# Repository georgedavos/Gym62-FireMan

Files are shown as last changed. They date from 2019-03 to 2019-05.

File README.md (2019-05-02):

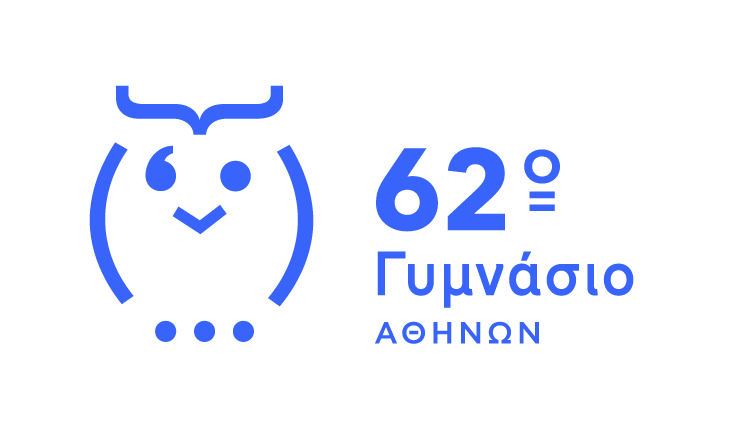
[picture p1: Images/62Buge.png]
62 Γυμνάσιο Αθηνών


# Gym62-FireMan
## Αυτόνομο Όχημα Ανίχνευσης Θέσης Πυρκαϊάς

Η ομάδα ρομποτικής του 62ου Γυμνασίου Αθηνών, μελετά και κατασκευάζει ένα  αυτοκινούμενο όχημα, το οποίο έχει ως σκοπό να επιτηρεί και να προστατεύει ένα δάσος από πυρκαϊά, και παράλληλα να μεταδίδει τα δεδομένα διαμέσου WiFi σημείου πρόσβασης που διαθέτει ενσωματωμένο.

Το Gym62-FireMan βασίστηκε σε ένα ερπυστριοφόρο σκάφος εκσκαφέα, το οποίο τροποποιήθηκε κατάλληλα για τις ανάγκες του έργου, ελάχιστης αξίας, και σε έναν ειδικό αισθητήρα παράταξης υπερύθρων ακτίνων. 

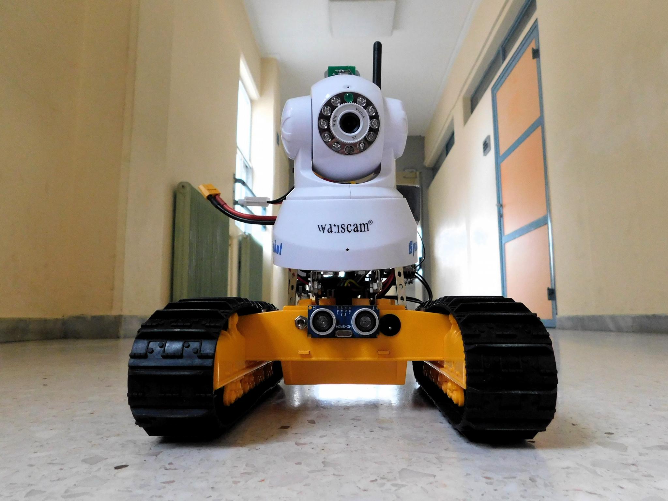
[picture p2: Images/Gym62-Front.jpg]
Gym62 Front


Gym62 Animated

## Περιγραφή πλοήγησης

 Το σύστημα βασίζεται σε ένα αισθητήρα παράταξης υπέρυθρων ακτίνων.
 
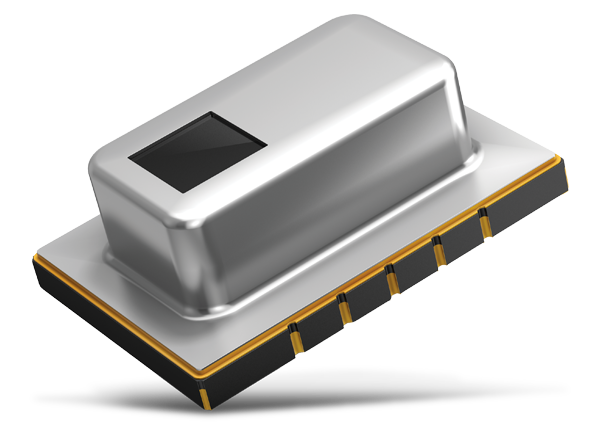
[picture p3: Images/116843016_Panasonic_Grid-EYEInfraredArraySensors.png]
Grid Eye
 
 
Ο αισθητήρας παράταξης είναι δομημένος σε ένα πίνακα 8*8 στοιχείων, δίνοντας 64 ανεξάρτητα σημεία μέτρησης της θερμότητας.
 Χωρίζοντας τον αισθητήρα σε 8 ζώνες ορίζοντα, ανιχνεύεται ο ορίζοντας στον οποίο εμφανίζεται η μέγιστη θερμότητα. Με βάση τον επιλεγμένο ορίζοντα, το όχημα μεταβάλει την ταχύτητα των ερπυστριών συνεχώς, αναλογικά σε σχέση πάντα με την θέση της μέγιστης θερμότητας στον επιλεγμένο ορίζοντα.
 Αυτή ή συνεχώς μεταβαλλόμενη ταχύτητα των ερπυστριών οδηγεί με μεγάλη ακρίβεια το όχημα στην θέση της πυρκαϊάς.   
 Πιο συγκεκριμένα το όχημα περιστρέφεται συνεχώς γύρω από τον εαυτό του μετρώντας τα θερμικά φορτία του πεδίου ορατότητας. Εάν κατά την περιστροφή, μετρηθεί θερμικό φορτίο μεγαλύτερο από το προκαθορισμένο ( Triger ), τότε σταματάει και κινείται προς αυτό, διορθώνοντάς συνεχώς την πορεία του φροντίζοντας να την διατηρεί σταθερή και ευθεία μπροστά με κέντρο πάντα το μέγιστο θερμικό φορτίο, επικοινωνώντας ταυτόχρονα με το κέντρο ελέγχου μεταδίδοντας σήματα σχετικά με τις λειτουργίες του και αποδέχεται ρυθμίσεις πλοήγησης.

## Λογισμικό Κέντρου Ελέγχου.
Το Gym62RCNT είναι μια εφαρμογή τηλεμετρίας για τον έλεγχο και της ρυθμίσεις του οχήματος.
Αναπτύσσεται σε περιβάλλον NetBeans 8.6 Java JDK 1.8.
Για να τρέξετε την εφαρμογή χωρίς την χρήση Του  NetBeans. Εγκαταστήστε το  java run time environment στο συστημά σας και τρέξτε το αρχείο  Gym62RCNT.jar

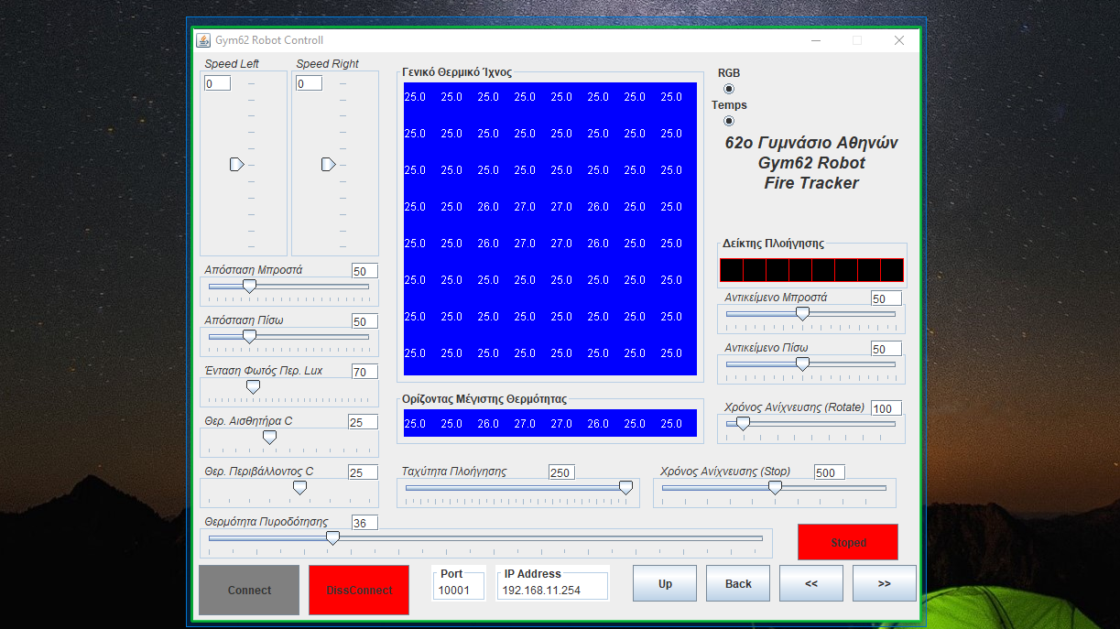
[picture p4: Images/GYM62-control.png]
Gym62 Control


## Κύκλωμα Gym62-MM3
Πρόκειται για ένα ηλεκτρονικό κύκλωμα επέκτασης οποιασδήποτε συμβατού Arduino πού λειτουργεί ως βάση σύνδεσης όλων των περιφερειακών συστημάτων τηλεμετρίας και τηλεκήνησης.
Για την ανάπτυξη του χρησιμοποιήθηκε το Ανοιχτό λογισμικό  KiCad IDE.

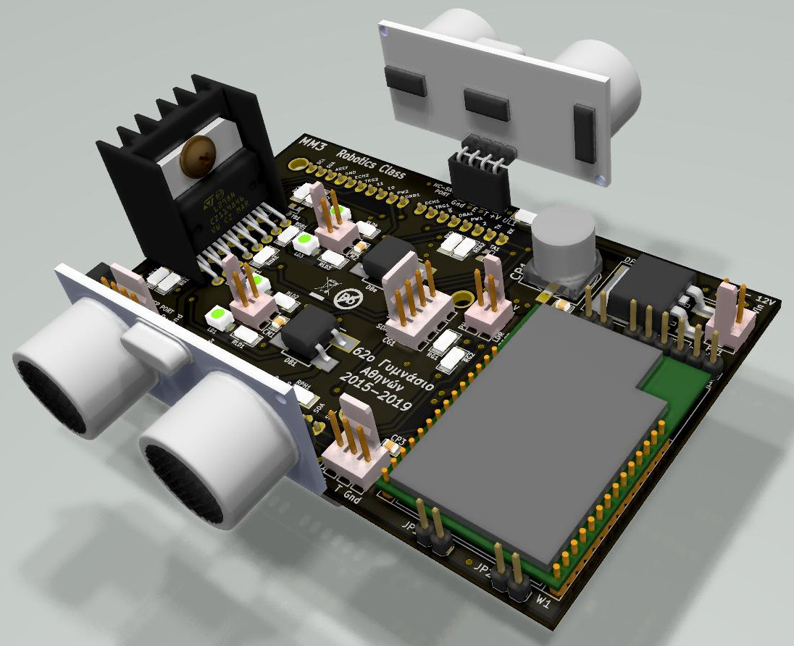
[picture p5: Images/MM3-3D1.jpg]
MM3-1


## Λεπτομέρεις Περιγραφές.
Περιγραφή περιεχομένων των αρχείων και των φακέλων που έχουν ενσωματωθεί στο github βρίσκεται σε αρχείο με όνομα "GYM62-FIREMAN-TreeOfFiles-Description" στον ίδιο κατάλογο με το παρόν ( https://github.com/georgedavos/Gym62-FireMan/blob/master/GYM62-FIREMAN-TreeOfFiles-Description.odt ).

Δείτε το βίντεο του έργου στο κανάλι youtube του σχολείου μας (62ο Γυμνάσιο Αθήνας)

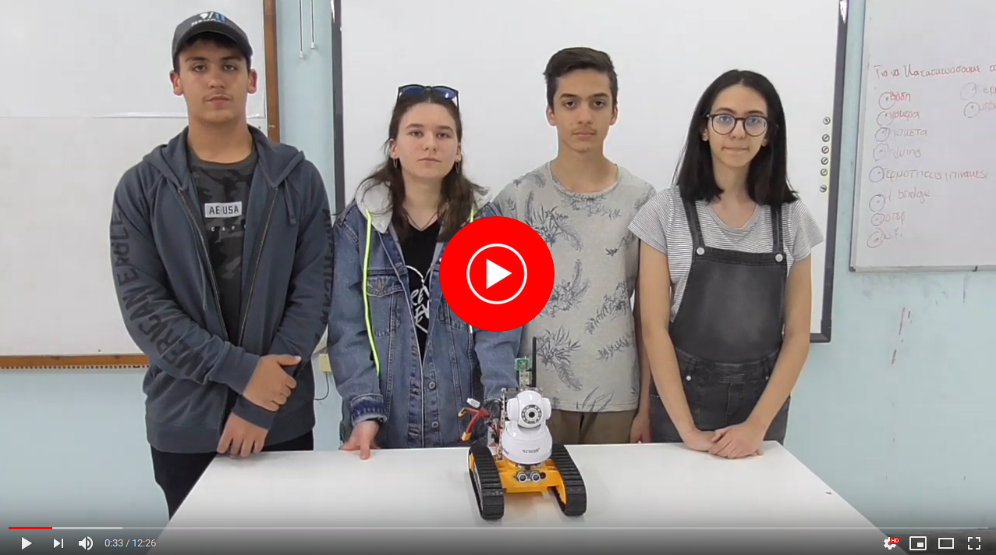
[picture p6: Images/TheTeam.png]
The Team (https://www.youtube.com/watch?v=zAY0CPyWmjs)


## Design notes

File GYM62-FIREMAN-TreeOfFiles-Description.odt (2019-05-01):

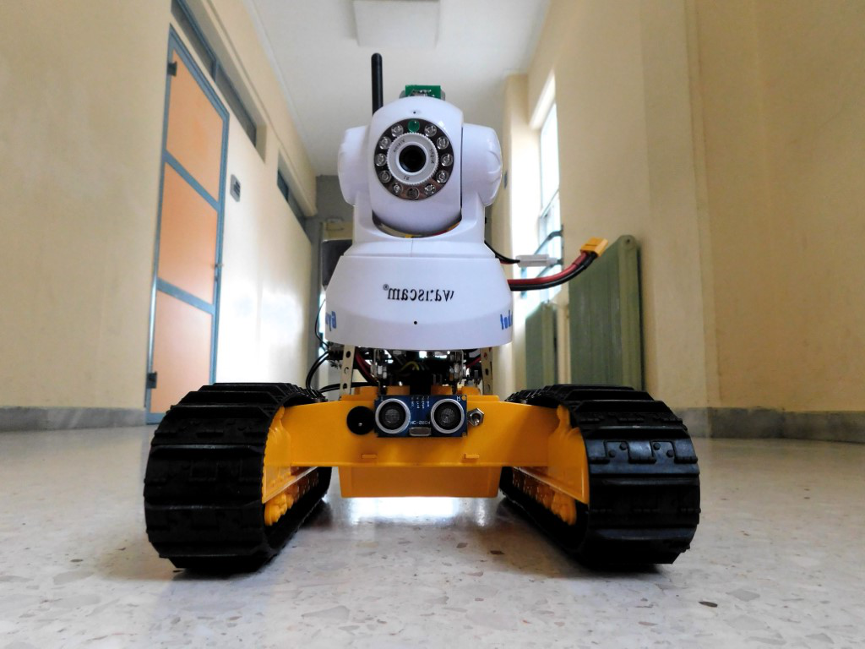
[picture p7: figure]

Περιγραφή δένδρου και σημαντικών αρχείων στο github του 62GYM-FIREMAN

Στο github του έργου (https://github.com/georgedavos/Gym62-FireMan)

Στον βασικό κατάλογο εμφανίζονται τα παρακάτω:

Αρχείο README.md είναι μια σύντομη περιγραφή του έργου που παρουσιάζεται.

Επίσης οι φάκελλοι:

- Arduino-Code/Gim62_MM3FireMan_A4 (https://github.com/georgedavos/Gym62-FireMan/tree/master/Arduino-Code/Gim62_MM3FireMan_A4) φάκελλος που περιέχει
- Το αρχείο Gim62_MM3FireMan_A4.ino (https://github.com/georgedavos/Gym62-FireMan/blob/master/Arduino-Code/Gim62_MM3FireMan_A4/Gim62_MM3FireMan_A4.ino) με τον πηγαίο κώδικα που έχει φορτωθεί στο Arduino με πλήρη σχόλια για κάθε λειτουργία που έχει ενσωματωθεί.
- Documents (https://github.com/georgedavos/Gym62-FireMan/tree/master/Documents) φάκελλος που περιέχει τις παρουσιάσεις και τις περιγραφές του έργου.
- Το αρχείο Περιγραφή Εργου Gym62-FireMan.odt (https://github.com/georgedavos/Gym62-FireMan/blob/master/Documents/Περιγραφή%20Εργου%20Gym62-FireMan.odt) έγγραφο με την γενική πιο λεπτομερή περιγραφή του έργου.
- Το αρχείο 62GYM-FIREMAN Κόστος Υλικών.odt (https://github.com/georgedavos/Gym62-FireMan/blob/master/Documents/62GYM-FIREMAN%20Κόστος%20Υλικών.odt) έγγραφο με το κόστος και την λεπτομερή λίστα των υλικών τόσο της πλακέτας GYM62-MM3 όσο και του συνολικού έργου.
- Το αρχείο Gym62-CameraDescription.odp (https://github.com/georgedavos/Gym62-FireMan/blob/master/Documents/Gym62-CameraDescription.odp) με την παρουσίαση των λειτουργιών και των τεχνικών χαρακτηριστικών της ενσωματωμένης κάμερας PLT-VGA
- To αρχείο Gym62-MM3_Description-final.odp (https://github.com/georgedavos/Gym62-FireMan/blob/master/Documents/Gym62-MM3_Description-final.odp) με την παρουσίαση των λειτουργιών και συνδέσεων της πλακέτας επέκτασης για ARDUINO GYM62-MM3 που έχει υλοποιηθεί στο σχολείο μας.
- Το αρχείο Gym62-WIFI&Αισθητήρας θερμότητας.odp (https://github.com/georgedavos/Gym62-FireMan/blob/master/Documents/Gym62-WIFI%26Αισθητήρας%20θερμότητας.odp) με την παρουσίαση των λειτουργιών της μονάδας WIFI και του αισθητήρα ανίχνευσης θερμικού φορτίου GRID EYE.
- Το αρχείο Gym62-Τηλεμετρία-Τηλεχειρισμός.odp (https://github.com/georgedavos/Gym62-FireMan/blob/master/Documents/Gym62-Τηλεμετρία-Τηλεχειρισμός.odp) με την παρουσίαση του κέντρου ελέγχου του ρομπότ της διαδικασίας της τηλεμετρίας και του τηλεχειρισμού του, όπως επίσης τα πρωτόκολλα που έχουν υλοποιηθεί για την μετάδοση δεδομένων από και προς το ρομπότ.
- Το αρχείο GYM62-FIREMAN-OER-ver2.pdf (https://github.com/georgedavos/Gym62-FireMan/blob/master/Documents/GYM62-FIREMAN-OER-ver2.pdf) που περιέχει τα στοιχεία του έργου με βάση το πρότυπο OER
- Gym62-MM3-Circuit (https://github.com/georgedavos/Gym62-FireMan/tree/master/Gym62-MM3-Circuit) φάκελλος που περιέχει:
    - MM3-Production (https://github.com/georgedavos/Gym62-FireMan/tree/master/Gym62-MM3-Circuit/MM3-Production) φάκελλος που περιέχει τα αρχεία σχεδιασμού της πλακέτας ως Project του KICAD ( EDA ) ( MM3.pro (https://github.com/georgedavos/Gym62-FireMan/blob/master/Gym62-MM3-Circuit/MM3.pro) ) ( MM3.sch (https://github.com/georgedavos/Gym62-FireMan/blob/master/Gym62-MM3-Circuit/MM3.sch) ) (MM3.kicad_pcb (https://github.com/georgedavos/Gym62-FireMan/blob/master/Gym62-MM3-Circuit/MM3.kicad_pcb)) και τα αρχεία GERBER για την παραγωγή της.
    - datasheets (https://github.com/georgedavos/Gym62-FireMan/tree/master/Gym62-MM3-Circuit/datasheets) : φάκελλος που περιέχει τα datasheets των βασικών εξαρτημάτων που χρησιμοποιήθηκαν – Είναι για τον μελλοντικό προγραμματιστή που θα βελτιώσει και θα αναπτύξει περαιτέρω το έργο
    - rescue-backup (https://github.com/georgedavos/Gym62-FireMan/tree/master/Gym62-MM3-Circuit/rescue-backup) : φάκελλος που το λέει και το όνομά του !!!!!
- Gym62RCNT (https://github.com/georgedavos/Gym62-FireMan/tree/master/Gym62RCNT) φάκελλος που περιέχει όλα τα αρχεία ανάπτυξης του κέντρου ελέγχου του ρομπότ ως Project σε ολοκληρωμένο περιβάλλον ανάπτυξης NetBeans IDE
- src (https://github.com/georgedavos/Gym62-FireMan/tree/master/Gym62RCNT/src) : φάκελλος που περιέχει τον source code σε Java της εφαρμογής του κέντρου ελέγχου
- Το αρχείο Gym62RCNT.jar (https://github.com/georgedavos/Gym62-FireMan/blob/master/Gym62RCNT/Gym62RCNT.jar) με την εφαρμογή του κέντρου ελέγχου υλοποιημένη σε JAVA
- Το αρχείο Gym62-Screen-Shot.jpg (https://github.com/georgedavos/Gym62-FireMan/blob/master/Gym62RCNT/Gym62-Screen-Shot.jpg) είναι μια φωτογραφία screenshot της εφαρμογής προς ενημέρωση
- Τα υπόλοιπα αρχεία και φάκελλοι είναι για τον προγραμματιστή της JAVA που θα βελτιώσει και θα αναπτύξει περαιτέρω το έργο (build (https://github.com/georgedavos/Gym62-FireMan/tree/master/Gym62RCNT/build), dist (https://github.com/georgedavos/Gym62-FireMan/tree/master/Gym62RCNT/dist), nbproject (https://github.com/georgedavos/Gym62-FireMan/tree/master/Gym62RCNT/nbproject) )
- Images (https://github.com/georgedavos/Gym62-FireMan/tree/master/Images) που περιέχει όλες τις φωτογραφίες που έχουν χρησιμοποιηθεί στα documents του έργου

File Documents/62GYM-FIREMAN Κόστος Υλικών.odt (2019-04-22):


Κόστος υλικών GYM62-FIREMAN

α/α | Περιγραφή Υλικού | Ενδεικτική τιμή λιανικής ( € )
1 | Όχημα ερπυστριοφόρο – μόνο το σκάφος από τροποποιημένο εκσκαφέα με λειτουργία των ερπυστριών και των μοτέρ τους, μικρής αξίας. | 15,00 €
2 | Arduino Uno ver3 | 7,00 €
3 | GYM62-MM3 Shield για το Arduino για εκπαιδευτικούς σκοπούς με την γέφυρα “Η” για τον έλεγχο των μοτέρ L298 DUAL FULL-BRIDGE DRIVER και λοιπά εξαρτήματα όπως περιγράφεται παρακάτω ** με υποδοχές για αισθητήρες για αποφυγή του πλήθους των καλωδιώσεων, σχεδιασμένο σε Kicad με πολύ χαμηλό κόστος παραγωγής. | 7,00 €
4 | Αναλογικός Αισθητήρας θερμοκρασίας περιβάλλοντος LM-35. | 0,40 €
5 | Αισθητήρας φωτός (φωτοαντίσταση LDR) | 0,50 €
6 | Αισθητήρας παράταξης υπερύθρων ακτίνων για την μέτρηση θερμότητας Grid Eye Panasonic. | 15,00 €
7 | Αισθητήρας Υπερήχων HC-SR 04 (2 τεμάχια) | 4,00 €
8 | Διεπαφή επικοινωνίας WIFI – Access Point HLK-RM 04 με την αντίστοιχη κεραία | 15,00 €
9 | Διεπαφή επικοινωνίας Bluetooth HC-06 (προαιρετική) | 2,50 €
10 | Web - Κάμερα μετάδοσης εικόνας Pan-Tilt-Zoom (κινούμενης κεφαλής) σε ανάλυση απλής VGA μικρής αξίας. | 25,00 €
11 | Μπαταρία Lipo 11,1V χαμηλού ρεύματος εκκίνησης | 28,00 €
12 | Στοιχεία μεταλλικών κατασκευών από παιχνίδια για τις στηρίξεις των υλικών | 3,00 €
13 | Καλώδια, ακροφύσια | 2,00 €
13 | Διακόπτες ηλεκτρικών και ηλεκτρονικών συνδέσεων. | 1,00 €
| ΣΥΝΟΛΟ | 106,4 €

Όλα τα υλικά αναφέρονται με λεπτομέρεια τόσο παρακάτω όσο και στα σχέδια της πλακέτας ΜΜ3 που έχουν μπεί στο github (https://github.com/georgedavos/Gym62-FireMan/tree/master/Gym62-MM3-Circuit/MM3-Production)του έργου (https://github.com/georgedavos/Gym62-FireMan/tree/master/Gym62-MM3-Circuit/MM3-Production) (https://github.com/georgedavos/Gym62-FireMan/tree/master/Gym62-MM3-Circuit/MM3-Production)

** Λίστα υλικών επί της πλακέτας επέκτασης στην επόμενη σελίδα μαζί με τους κατασκευαστές κάθε είδους

** Υλικά πλακέτας 62GYM-MM3 Shield

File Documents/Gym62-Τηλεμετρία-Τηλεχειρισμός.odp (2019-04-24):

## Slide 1

η ομαδα ρομποτικησ στο


παρουσιαζει

Gym62_FireMan

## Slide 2

Gym62_Robot

Gym62_FireMan

Gym62_FireMan

ΠΕΡΙΓΡΑΦΗ κεντρου ελεγχου και πρωτοκολλου επικοινωνιασ

Μαθητές:

Βενέτης Αναστάσης

Μαλανκά Αλεξάνδρα

Παναγιωτάκης Βαγγέλης

Σπυροπούλου Ζωή

Καθηγητές-Μέντορες:

Δάβος Γεώργιος

Βλαστός Αθανάσιος

Μπερερής Σπύρος

## Λειτουργία και πρωτόκολλο επικοινωνίας

Gym62_Robot

- Το ρομπότ μας επικοινωνεί με κέντρο ελέγχου τηλεμετρίας και τηλεχειρισμού, που εκτελείται σε ένα laptop ή σε desktop με ασύρματη κάρτα δικτύου.
- Ο κάθε χείριστης του ρομπότ μπορεί να λαμβάνει δεδομένα από το ρομπότ αλλά και να ρυθμίζει τις λειτουργίες του μέσα από ένα πρόγραμμα σε Java που έχουμε δημιουργήσει με την βοήθεια του μέντορά μας Βλαστού Αθανάσιου.
- Η μετάδοση των δεδομένων από και προς το κέντρο ελέγχου γίνεται μέσω πρωτοκόλλου μετάδοσης data που σχεδιάστηκε ειδικά για το Gym62-Fireman

Gym62_FireMan

## Τηλεμετρία

Gym62_Robot

  Το ρομπότ επικοινωνεί με τον πίνακα ελέγχου και στέλνει πληροφορίες η οποίες αφορούν την λειτουργία του :
- Ταχύτητα και κατεύθυνση (δεξιάς και αριστερής ερπύστριας)
- Θερμοκρασία περιβάλλοντος του ρομπότ
- Απόσταση από εμπόδια (αισθητήρας υπερήχων μπροστά και πίσω)
- Φωτεινότητα περιβάλλοντος
- Θερμοκρασίες που ανιχνεύει ο θερμικός ανιχνευτής GridEye
- Δείκτης αυτόματης πλοήγησης – κατεύθυνσης κίνησης

Gym62_FireMan

## Τηλεχειρισμός

Gym62_Robot

  Μέσω του πίνακα ελέγχου μπορεί κανείς να ελέγξει κάποιες λειτουργίες του ρομπότ χωρίς αλλαγή στον κώδικα :
- Ταχύτητα και κατεύθυνση ερπυστριών σε ποσοστό – σημειώνεται ότι αρνητικές τιμές σημαίνει κίνηση προς τα πίσω και θετικές κίνηση εμπρός.
- Ρύθμιση χρόνου ταχύτητας περιστροφής στην φάση ανίχνευσης
- Κατώφλι Θερμοκρασίας ανίχνευσης

Gym62_FireMan

## Τηλεκίνηση

Gym62_Robot

  Το ρομπότ σταματάει να ακολουθεί το πρόγραμμα και μπορεί να ελεγχθεί η κατεύθυνση του από τον πινάκα ελέγχου . Οι κινήσεις που μπορεί να εκτελέσει ρυθμίζοντας το είδος της κίνησης και την ταχύτητα κίνησης των ερπυστριών είναι οι εξής
- Μπροστά (θετικές τιμές)
- Πίσω (αρνητικές τιμές)
- Γύρω από τον άξονα του, δεξιά (αντίστροφη κίνηση ερπυστριών)
- Γύρω από τον άξονα του, αριστερά (αντίστροφη κίνηση ερπυστριών)

Gym62_FireMan

## Πρωτόκολλο επικοινωνίας Τηλεμετρίας

Gym62_Robot

  Η μετάδοση των δεδομένων από το ρομπότ προς το κέντρο ελέγχου ασύρματα γίνεται, όπως φαίνεται και στον ενσωματωμένο σχολιασμό του κώδικα, με τη χρήση strings μέσω πακέτων μετάδοσης του προτύπου UART του TCP/IP. Aνάλογα με το είδος των δεδομένων ξεκινούν με:
1. !tmp- : Θερμοκρασία
2. !lgt- : Φωτεινότητα
3. !spr- & !spl- :Ταχύτητα δεξιάς & αριστερής ερπύστριας σε ποσοστό επί της ισχύος του μοτέρ
4. !dtf- & !dtb- : Αποστάσεις μπροστά & πίσω αισθητήρα υπερήχων σε cm
5. !htt- : Θερμοκρασία του περιβάλλοντος του Ρομπότ
  και ακολουθούν μετά από αυτά οι αντίστοιχες τιμές πχ ‘!tmp-22’

Gym62_FireMan

## Πρωτόκολλο επικοινωνίας Τηλεχειρισμού

Gym62_Robot

Gym62_FireMan

  Η μετάδοση των δεδομένων από το κέντρο ελέγχου προς το ρομπότ ασύρματα γίνεται όπως φαίνεται και στον ενσωματωμένο σχολιασμό του κώδικα με τη χρήση strings μέσω πακέτων μετάδοσης του προτύπου UART του TCP/IP. Aνάλογα με το είδος των δεδομένων ξεκινούν με:
- !spd- :Ταχύτητα Ρομπότ σε ποσοστό της ισχύος του μοτέρ (50%)
- !tme- : Χρονόμετρο σε sec
- !trg- : Κατώφλι Θερμοκρασίας ανίχνευσης θερμικού στόχου σε oC
  και ακολουθούν μετά από αυτά οι αντίστοιχες τιμές πχ ‘!spd-50’

## Πίνακας ελέγχου (Τηλεμετρία)

Gym62_Robot

Gym62_FireMan

1.Θερμοκρασία περιβάλλοντος

2.Φωτεινότητα περιβάλλοντος

3.Ταχύτητα και φορά δεξιάς & αριστερής ερπύστριας (+ ή -% )

4.Αποστάσεις μπροστά & πίσω αισθητήρα

5.Θερμοκρασία περιβάλλοντος (του Ρομπότ)

3

4

2

5

1

## Πίνακας ελέγχου (Τηλεδιαχείριση)

Gym62_Robot

Gym62_FireMan

1.Ταχύτητα κίνησης Ρομπότ (0-255)

2.Χρόνος ρύθμισης ταχύτητας περιστροφής στη φάση Ανίχνευσης

3.Κατώφλι Θερμοκρασίας που θα ανιχνεύει το ρομπότ

4. Κουμπί εκκίνησης και στάσης του ρομπότ με αλλαγή χρώματος και λεζάντας σε λειτουργία

5. Εισαγωγή διεύθυνσης IP του ρομπότ και πόρτας μετάδοσης δεδομένων

6. Κουμπιά σύνδεσης και αποσύνδεσης με το ρομπότ με αλλαγή χρώματος και λεζάντας

1

2

3

4

5

6

## Πίνακας ελέγχου (Τηλεχειρισμός κίνησης)

Gym62_Robot

Gym62_FireMan

Όταν το ρομπότ δεν είναι σε φάση ανίχνευσης (stopped mode) τότε μπορούμε να διαχειριστούμε την κίνησή του

1.φάση stpped mode – δεν ανιχνεύει φωτιά

2.Κουμπιά χειρισμού της κίνησης με τη σειρά μπρός (up), πίσω back), αριστερά (<<) και δεξιά (>>)

1

2

## Πίνακας ελέγχου (Grid Eye)

Gym62_Robot

Gym62_FireMan

1.Τιμές θερμικού ανιχνευτή (Grid Eye) και γραμμή μέγιστων θερμοκρασιών (Ορίζοντας Μέγιστης Θερμότητας)

2.Δείκτης πλοήγησης – κατεύθυνσης κίνησης (auto navigation feedback)

1

2

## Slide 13

Gym62_Robot

Gym62_FireMan

ΕΥΧΑΡΙΣΤΟΥΜΕ

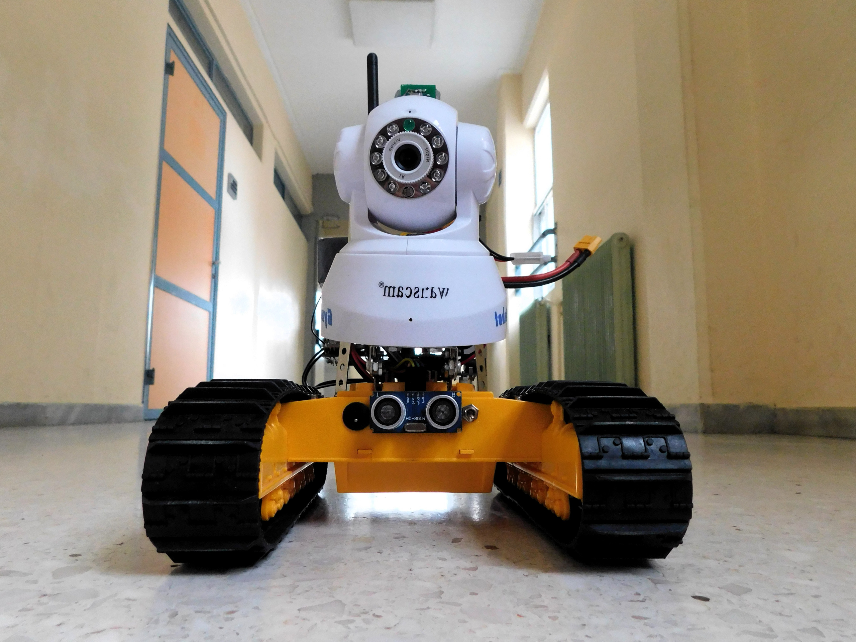
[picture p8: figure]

Η ΟΜΑΔΑ ΡΟΜΠΟΤΙΚΗΣ ΜΑΣ

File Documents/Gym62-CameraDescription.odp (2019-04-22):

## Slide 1

η ομαδα ρομποτικησ στο


παρουσιαζει

Gym62_FireMan

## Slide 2

Gym62_Robot

Gym62_FireMan

ΠΕΡΙΓΡΑΦΗ ΚΑΜΕΡΑΣ

Μαθητές:

Βενέτης Αναστάσης

Μαλανκά Αλεξάνδρα

Παναγιωτάκης Βαγγέλης

Σπυροπούλου Ζωή

Καθηγητές-Μέντορες:

Δάβος Γεώργιος

Βλαστός Αθανάσιος

Μπερερής Σπύρος

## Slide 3

Gym62_Robot

Gym62_FireMan

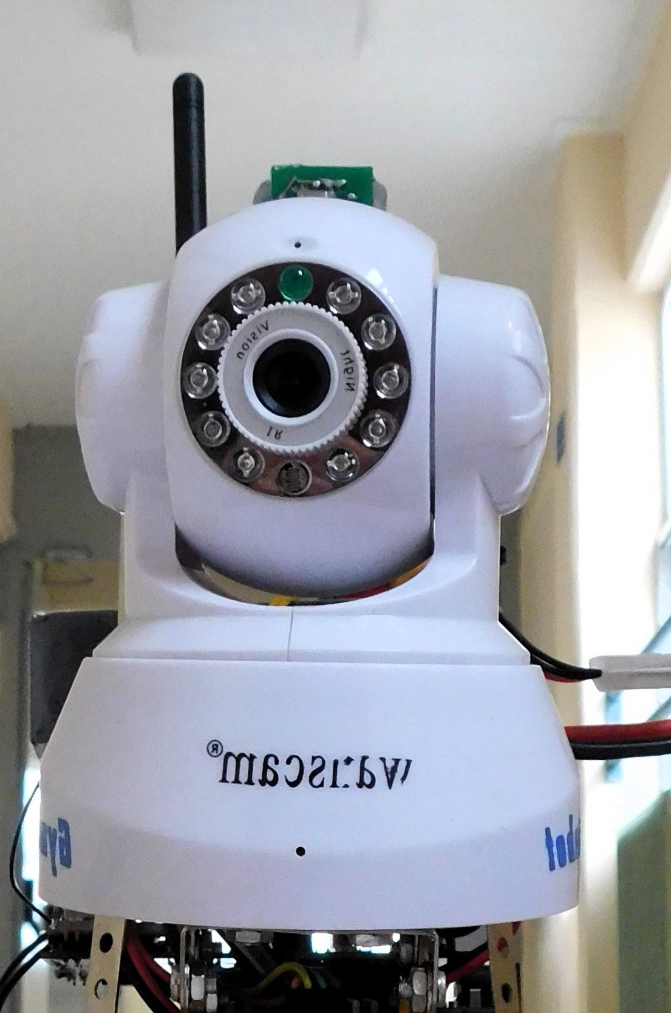
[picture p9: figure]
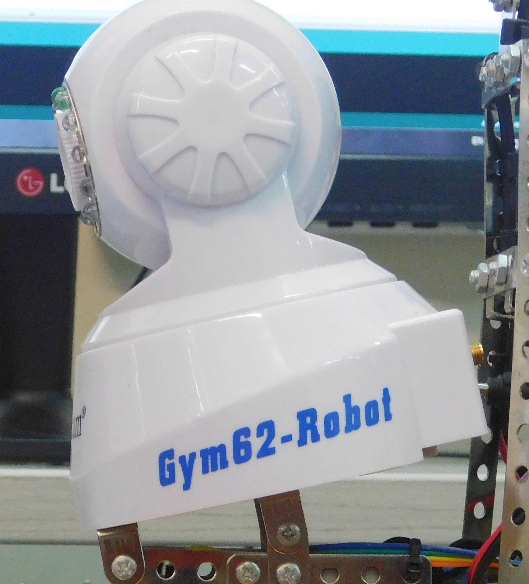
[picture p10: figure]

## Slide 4

Gym62_Robot

Gym62_FireMan

Γενικά

Η κάμερα τοποθετήθηκε στο Gym62_Fireman για την λήψη απευθείας εικόνας από το σημείο που βρίσκεται το ρομπότ. Κάθε χειριστής του ρομπότ μπορεί να έχει εικόνα της κάμερας μέσω WIFI σε ζωντανή μετάδοση.

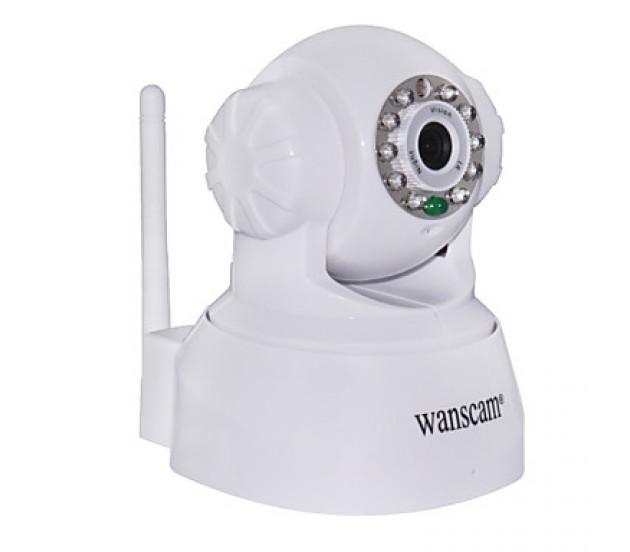
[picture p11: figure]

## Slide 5

Gym62_Robot

Gym62_FireMan

Χαρακτηριστικά

Μοντέλο:

Indoor Pan-Tilt-Zoom IP surveillance camera day night wireless

IP: 192.168.11.101

Θύρα: 99

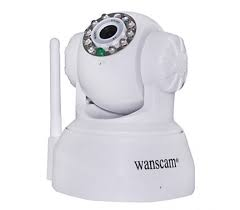
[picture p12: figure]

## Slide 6

Gym62_Robot

Gym62_FireMan

ΕΥΧΑΡΙΣΤΟΥΜΕ


Η ΟΜΑΔΑ ΡΟΜΠΟΤΙΚΗΣ ΜΑΣ

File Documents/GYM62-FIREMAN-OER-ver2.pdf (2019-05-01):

## Η ΠΗΓΗ ΔΙΔΑΣΚΑΛΙΑΣ

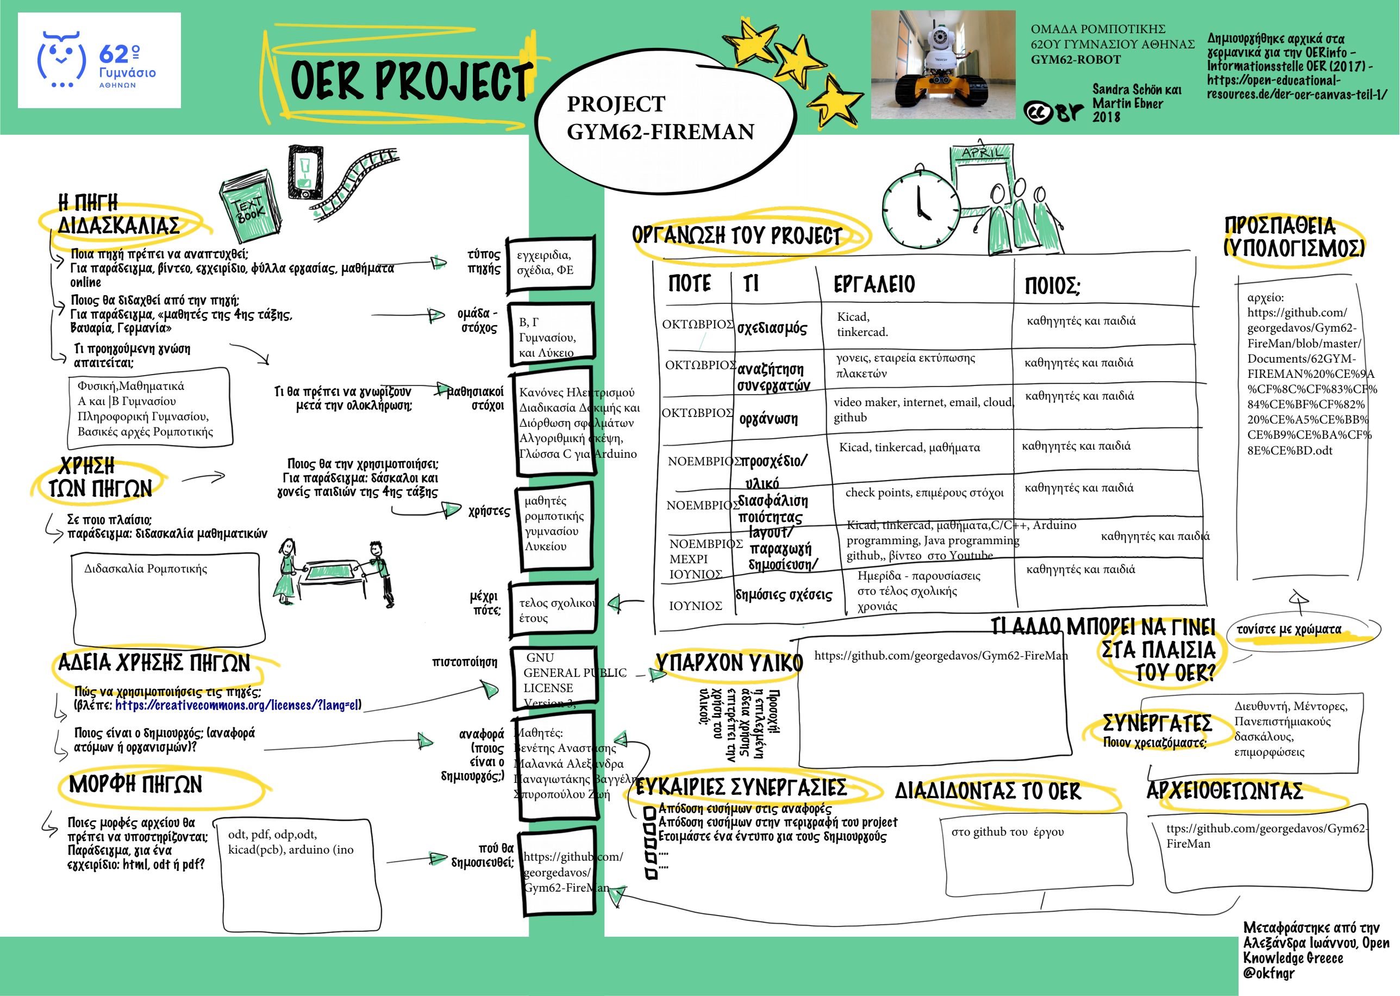
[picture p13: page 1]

τύπος
πηγής

# OER PROJECT

ομάδα -
στόχος

μαθησιακοί
στόχοι

μέχρι
πότε;

πιστοποίηση

χρήστες

αναφορά
(ποιος
είναι ο
δημιουργός;)

πού θα
δημοσιευθεί;

## ΜΟΡΦΗ ΠΗΓΩΝ

## ΧΡΗΣΗ ΤΩΝ ΠΗΓΩΝ

ΑΔΕΙΑ ΧΡΗΣΗΣ ΠΗΓΩΝ | ΥΠΑΡΧΟΝ ΥΛΙΚΟ

## ΠΡΟΣΠΑΘΕΙΑ (ΥΠΟΛΟΓΙΣΜΟΣ)

## ΤΙ ΑΛΛΟ ΜΠΟΡΕΙ ΝΑ ΓΙΝΕΙ ΣΤΑ ΠΛΑΙΣΙΑ ΤΟΥ OER?

## ΕΥΚΑΙΡΙΕΣ ΣΥΝΕΡΓΑΣΙΕΣ

ΠΟΤΕ | ΕΡΓΑΛΕΙΟ | ΠΟΙΟΣ;
ΔΙΑΔΙΔΟΝΤΑΣ ΤΟ OER | ΑΡΧΕΙΟΘΕΤΩΝΤΑΣ

## ΟΡΓΑΝΩΣΗ ΤΟΥ PROJECT

Ποια πηγή πρέπει να αναπτυχθεί;
Για παράδειγμα, βίντεο, εγχειρίδιο, φύλλα εργασίας, μαθήματα online
Ποιος θα διδαχθεί από την πηγή;
Για παράδειγμα, «μαθητές της 4ης τάξης,
Βαυαρία, Γερμανία»
Τι προηγούμενη γνώση
απαιτείται;

Τι θα πρέπει να γνωρίζουν
μετά την ολοκλήρωση;

Ποιος θα την χρησιμοποιήσει; Για παράδειγμα: δάσκαλοι και γονείς παιδιών της 4ης τάξης

Σε ποιο πλαίσιο;
παράδειγμα: διδασκαλία μαθηματικών

Πώς να χρησιμοποιήσεις τις πηγές;
(βλέπε: https://creativecommons.org/licenses/?lang=el)

Ποιος είναι ο δημιουργός; (αναφορά
ατόμων ή οργανισμών)?

## ΣΥΝΕΡΓΑΤΕΣ

Ποιον χρειαζόμαστε;

Ποιες μορφές αρχείου θα
πρέπει να υποστηρίζονται;
Παράδειγμα, για ένα
εγχειρίδιο: html, odt ή pdf?

Απόδοση ευσήμων στις αναφορές
Απόδοση ευσήμων στην περιγραφή του project Ετοιμάστε ένα έντυπο για τους δημιουργούς ….
….

Προσοχ

ή!

η επιλεγμέν

η

άδεια

χρή

σ
η
ς

επιτρέπει τ

η
ν

χρή

σ
η
του

υ
λικού;

σχεδιασμός

αναζήτηση
συνεργατών

οργάνωση

προσχέδιο/
υλικό
διασφάλιση
ποιότητας
layout/
παραγωγή
δημοσίευση/

δημόσιες σχέσεις

ΤΙ

τονίστε με χρώματα

Sandra Schön και
Martin Ebner
2018

Δημιουργήθηκε αρχικά στα
γερμανικά για την OERinfo – Informationsstelle OER (2017) -https://open-educational-resources.de/der-oer-canvas-teil-1/

Μεταφράστηκε από την
Αλεξάνδρα Ιωάννου, Open
Knowledge Greece
@okfngr

εγχειριδια,
σχέδια, ΦΕ

Β, Γ
Γυμνασίου,
και Λύκειο

Φυσική,Μαθηματικά
Α και |Β Γυμνασίου
Πληροφορική Γυμνασίου,
Βασικές αρχές Ρομποτικής

Κανόνες Ηλεκτρισμού
Διαδικασία Δοκιμής και
Διόρθωση σφαλμάτων
Αλγοριθμική σκέψη,
Γλώσσα C για Arduino

τελος σχολικού
έτους

GNU
GENERAL PUBLIC
LICENSE
Version 3,
Μαθητές:
Βενέτης Αναστάσης
Μαλανκά Αλεξάνδρα
Παναγιωτάκης Βαγγέλης
Σπυροπούλου Ζωή

https://github.com/
georgedavos/
Gym62-FireMan

Διδασκαλία Ρομποτικής

odt, pdf, odp,odt,
kicad(pcb), arduino (ino

ΟΚΤΩΒΡΙΟΣ

ΟΚΤΩΒΡΙΟΣ

ΟΚΤΩΒΡΙΟΣ

ΝΟΕΜΒΡΙΟΣ

ΝΟΕΜΒΡΙΟΣ

ΝΟΕΜΒΡΙΟΣ
ΜΕΧΡΙ
ΙΟΥΝΙΟΣ

ΙΟΥΝΙΟΣ

Kicad,
tinkercad.
γονεις, εταιρεία εκτύπωσης πλακετών
video maker, internet, email, cloud, github
Kicad, tinkercad, μαθήματα

check points, επιμέρους στόχοι

Kicad, tinkercad, μαθήματα,C/C++, Arduino programming, Java programming github,, βίντεο στο Youtube
Ημερίδα - παρουσίασεις
στο τέλος σχολικής
χρονιάς

καθηγητές και παιδιά

καθηγητές και παιδιά

καθηγητές και παιδιά

καθηγητές και παιδιά

καθηγητές και παιδιά

καθηγητές και παιδιά

καθηγητές και παιδιά

https://github.com/georgedavos/Gym62-FireMan

Διευθυντή, Μέντορες,
Πανεπιστήμιακούς
δασκάλους,
επιμορφώσεις

αρχείο:
https://github.com/
georgedavos/Gym62-
FireMan/blob/master/
Documents/62GYM-FIREMAN%20%CE%9A
%CF%8C%CF%83%CF%
84%CE%BF%CF%82%
20%CE%A5%CE%BB%
CE%B9%CE%BA%CF%
8E%CE%BD.odt

στο github του έργου

ttps://github.com/georgedavos/Gym62-FireMan

μαθητές
ρομποτικής
γυμνασίου
Λυκείου

ΟΜΑΔΑ ΡΟΜΠΟΤΙΚΗΣ
62ΟΥ ΓΥΜΝAΣΙΟΥ ΑΘΗΝΑΣ
GYM62-ROBOT

# PROJECT GYM62-FIREMAN

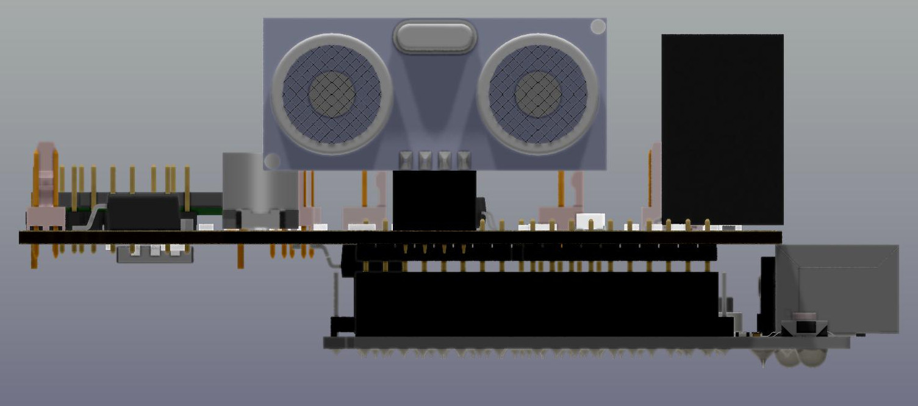
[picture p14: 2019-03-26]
Images/MM3-3D3.jpg

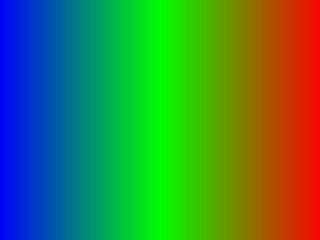
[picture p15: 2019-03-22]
Gym62RCNT/src/images/rgb.jpg

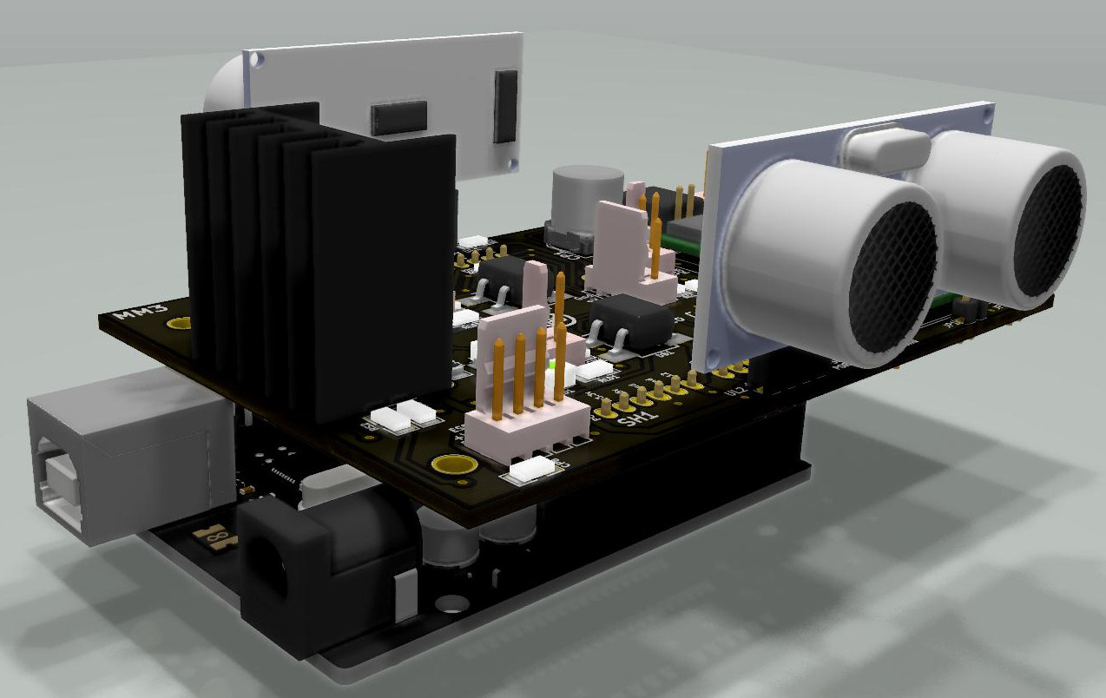
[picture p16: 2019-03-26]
Images/MM3-3D2.jpg

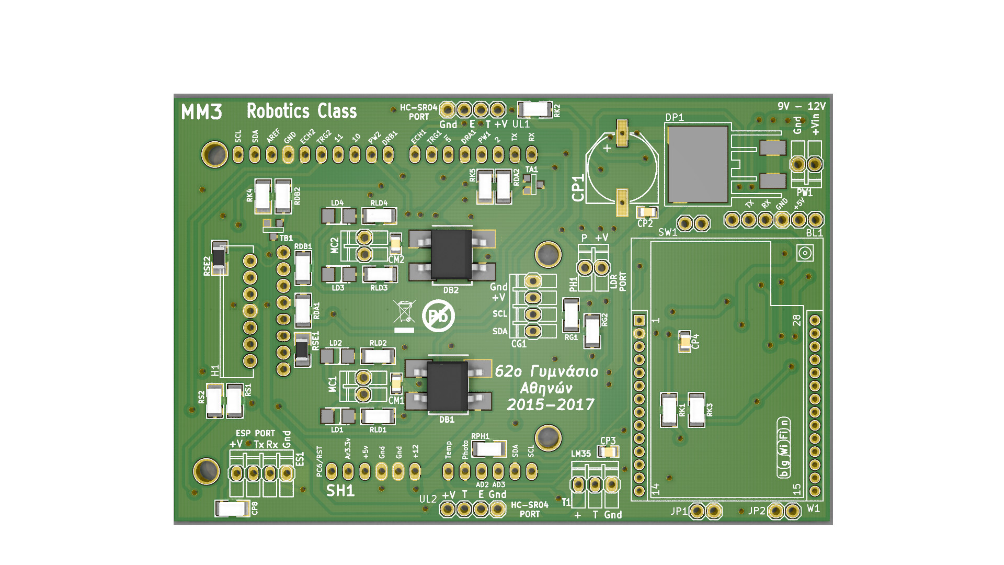
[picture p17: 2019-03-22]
Gym62-MM3-Circuit/MM3-Production/PCB.jpg

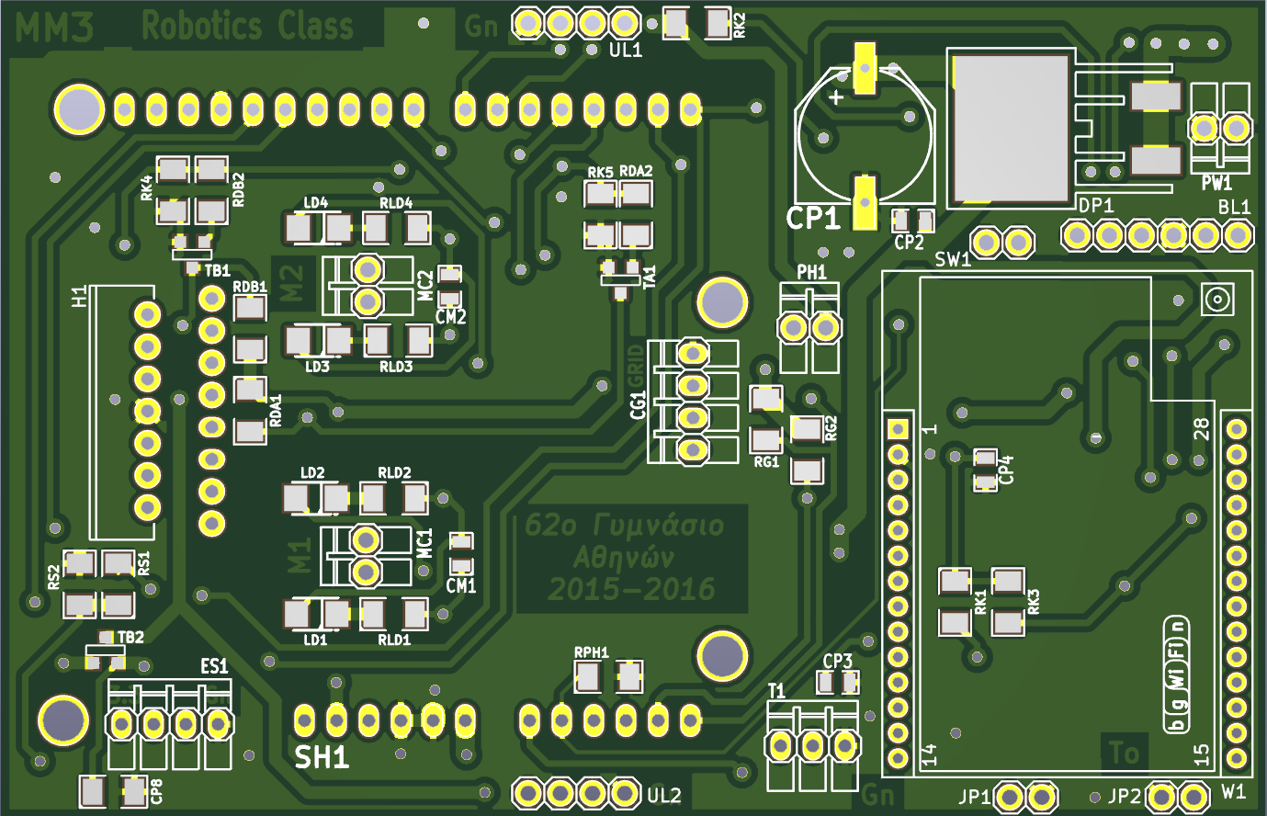
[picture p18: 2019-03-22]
Gym62-MM3-Circuit/MM3-Production/MM3.png

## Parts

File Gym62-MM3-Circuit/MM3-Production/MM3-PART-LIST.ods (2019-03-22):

Gym62 Robot MM3 Circuit Part List
Type | Designator | Package | Quantity | Designation | Supplier and ref
Resistor | RS2 | SM 1206 | 1 | 2K | Any
WiFi Module | W1 | HLK-RM04 | 1 | HLK-RM04 | Hi-LINK
Pins | CG1,ES1 | PIN HEADER 2.54mm | 2 | 4p | Any
Capacitors Ceramic | CM1,CM2,CP2,CP3,CP4,CP5,CP6 | SM 0805 | 7 | 100n 50V | Any
Capacitors Electrolytic | CP1 | CAP-SMD-TYPE F | 1 | 220uF 16V | EEEFK1E221P panasonic or equivalent
Diode | DP1 | AV-D2PACK | 1 | 12CWQ06FN | Vishay
LED | LD1,LD3 | PLCC2 | 2 | RED LED | Any 3528 LED
LED | LD2,LD4 | PLCC2 | 2 | YELLOW LED | Any 3528 LED
Resistor | RLD1,RLD2,RLD3,RLD4 | SM 1206 | 4 | 4.7K | Any
Pins | MC1,MC2,PW1 | PIN HEADER 2.54mm | 3 | 2P | Any
Resistor | RG1,RG2 | SM 1206 | 2 | 3.3k | Any
Jumpers/Switch | JP1,JP2,SW1 | PIN HEADER 2.54mm | 3 | jp | Any
Light Dependent Resistor | PH1 | Radial | 1 | LDR | Any
Resistor | RK1,RK2,RK3 | SM 1206 | 3 | 10k | Any
Resistor | RPH1 | SM 1206 | 1 | 4.7k | Any
Thermometer | T1 | TO-92 | 1 | LM35 | Ti
Pins | UL1,UL2 | PIN HEADER 2.54mm | 2 | 4p | Any
Pins | BL1 | PIN HEADER 2.54mm | 1 | 6p | Any
H Bridge | H1 | Multiwat15V | 1 | L298N | ST
Resistor | RDA1,RDA2,RDB1,RDB2 | SM 1206 | 4 | 3.3K | Any
Regulator | REG1 | DPAK3 | 1 | LM1086-IS-5 | Ti
Resistor | RK4,RK5 | SM 1206 | 2 | 10K | Any
Resistor | RS1 | SM 1206 | 1 | 1K | Any
Transistor | TB1,TA1 | SOT23M | 2 | BC817 | OnSemi
Capacitor Ceramic | CP7,CP8 | SM 1206 | 2 | 47uf | Any
Resistor | RSE1,RSE2 | SM 1206 | 2 | 0,5 | Any
Capacitor Ceramic | CP9,CP10 | SM 0805 | 2 | 100n 50V | Any
Regulator | REG2 | DPAK3 | 1 | LM1086-IS-3.3 | Ti
Diode Bridge Rectifier | DB1,DB2 | Bridge-SMD | 2 | DF10S | Vishay

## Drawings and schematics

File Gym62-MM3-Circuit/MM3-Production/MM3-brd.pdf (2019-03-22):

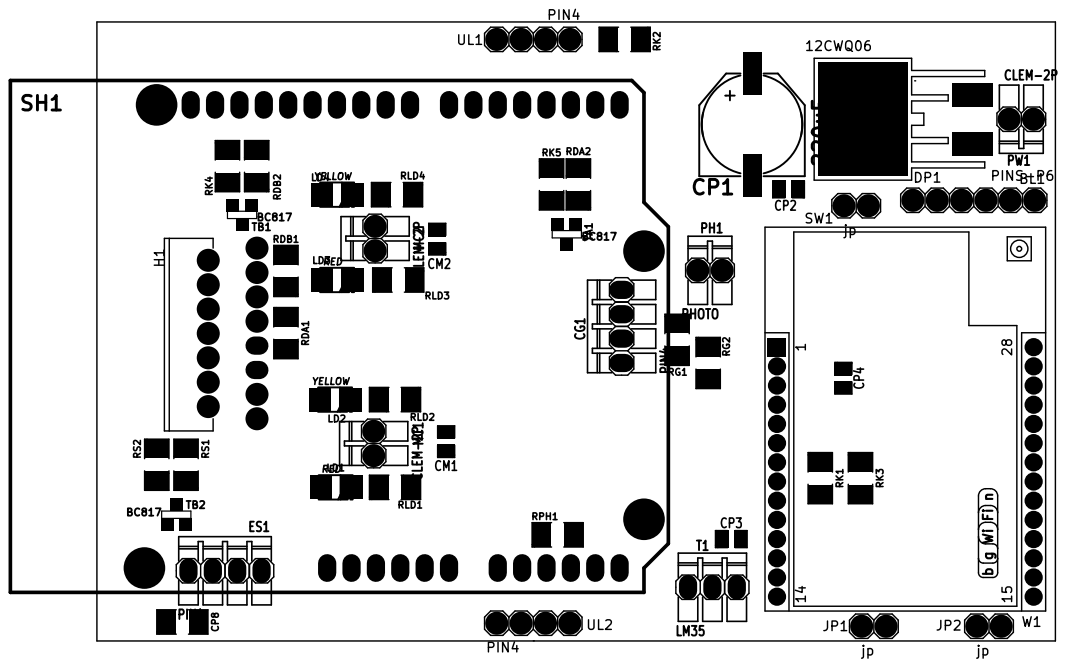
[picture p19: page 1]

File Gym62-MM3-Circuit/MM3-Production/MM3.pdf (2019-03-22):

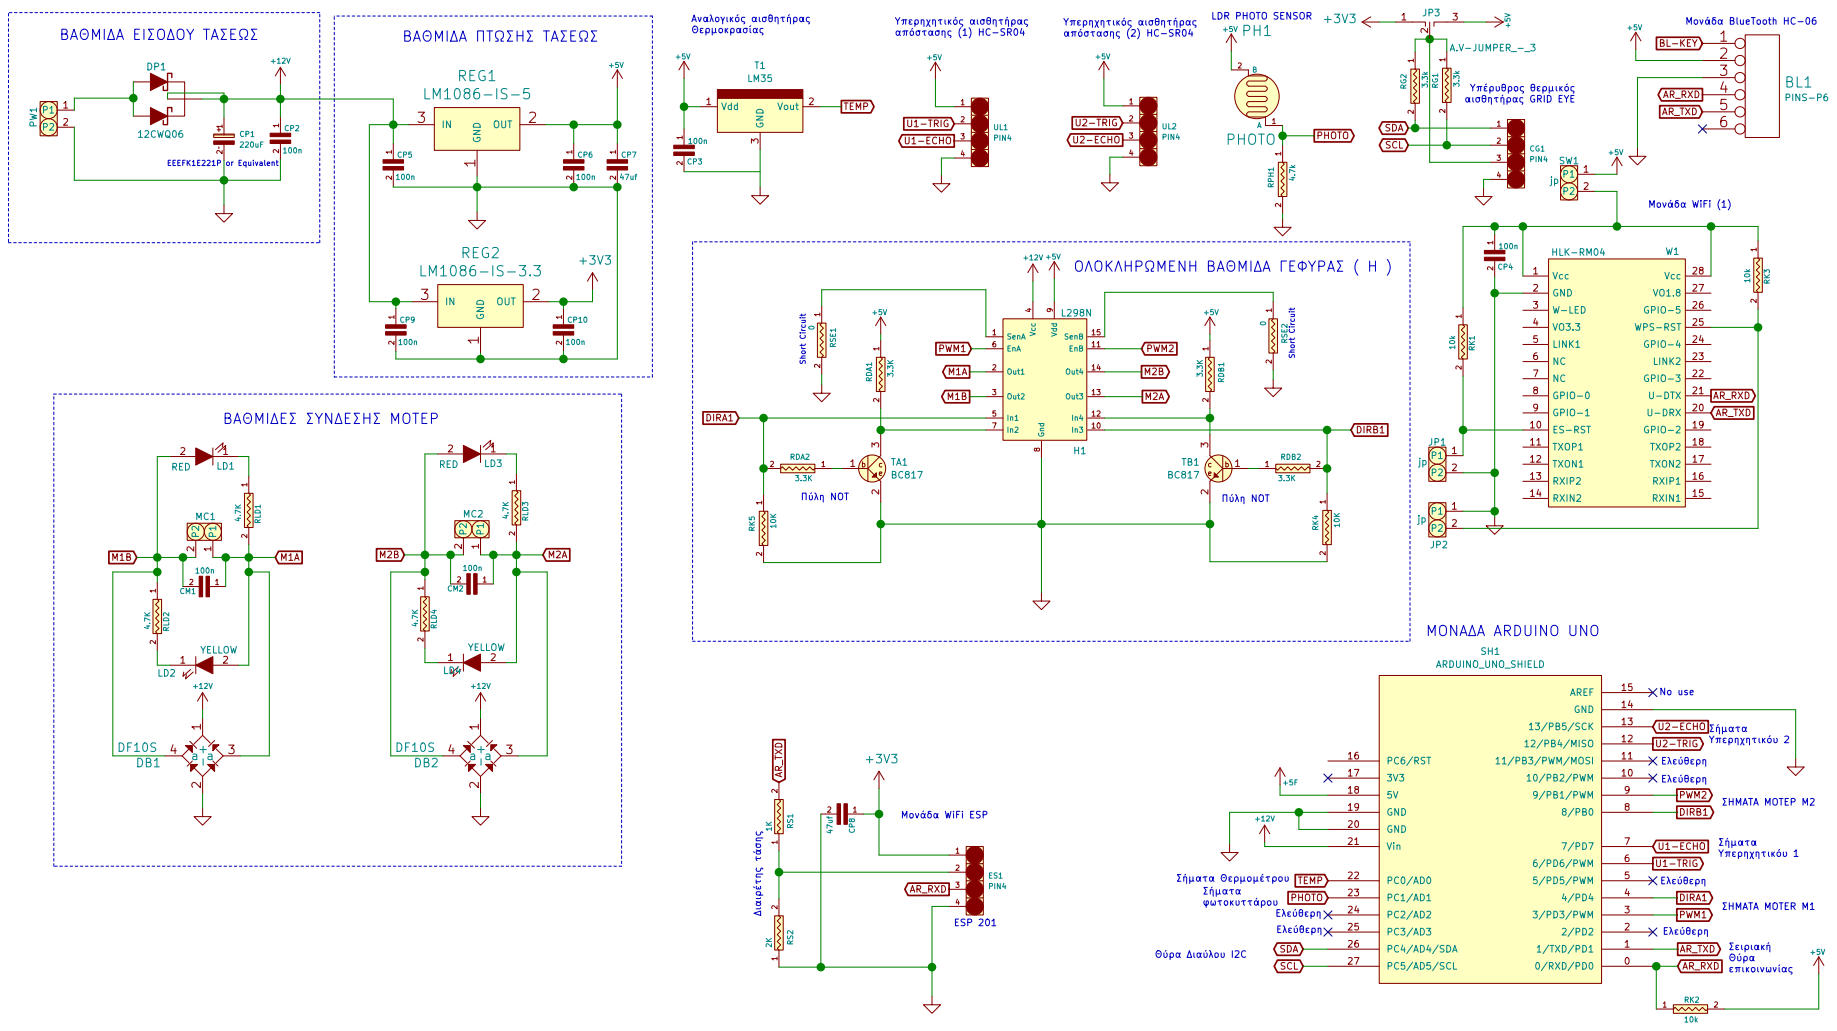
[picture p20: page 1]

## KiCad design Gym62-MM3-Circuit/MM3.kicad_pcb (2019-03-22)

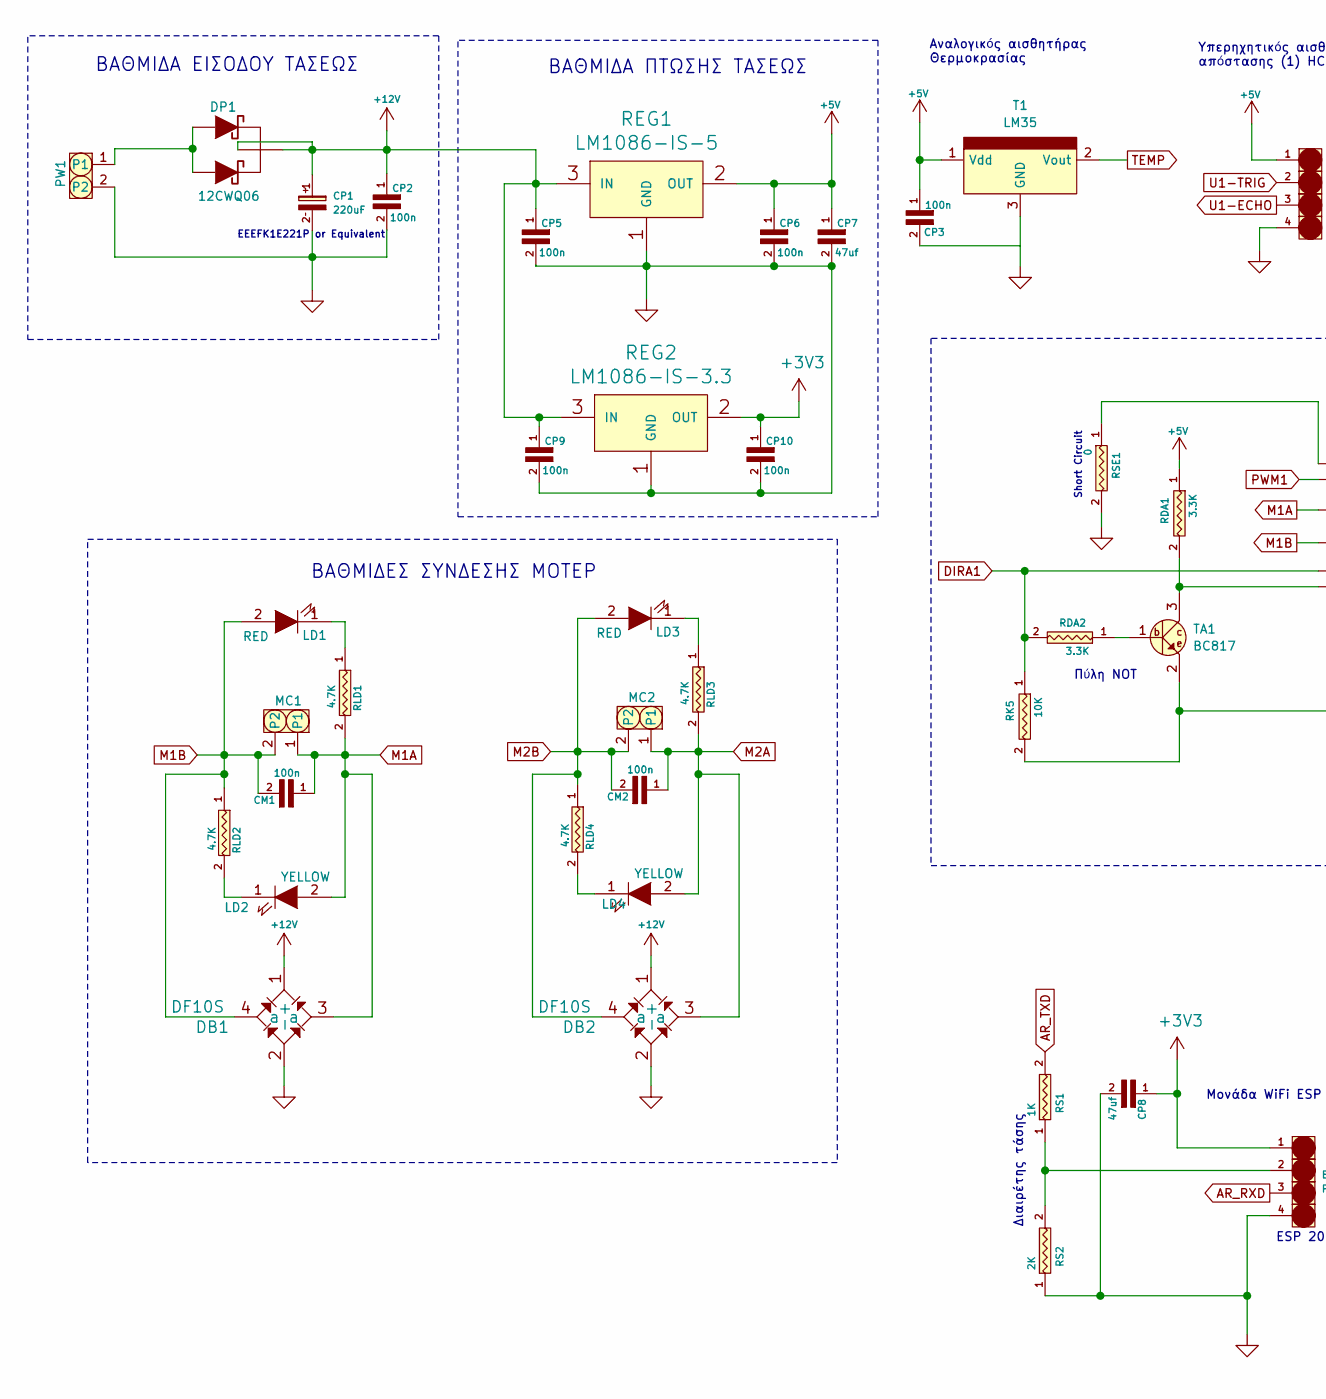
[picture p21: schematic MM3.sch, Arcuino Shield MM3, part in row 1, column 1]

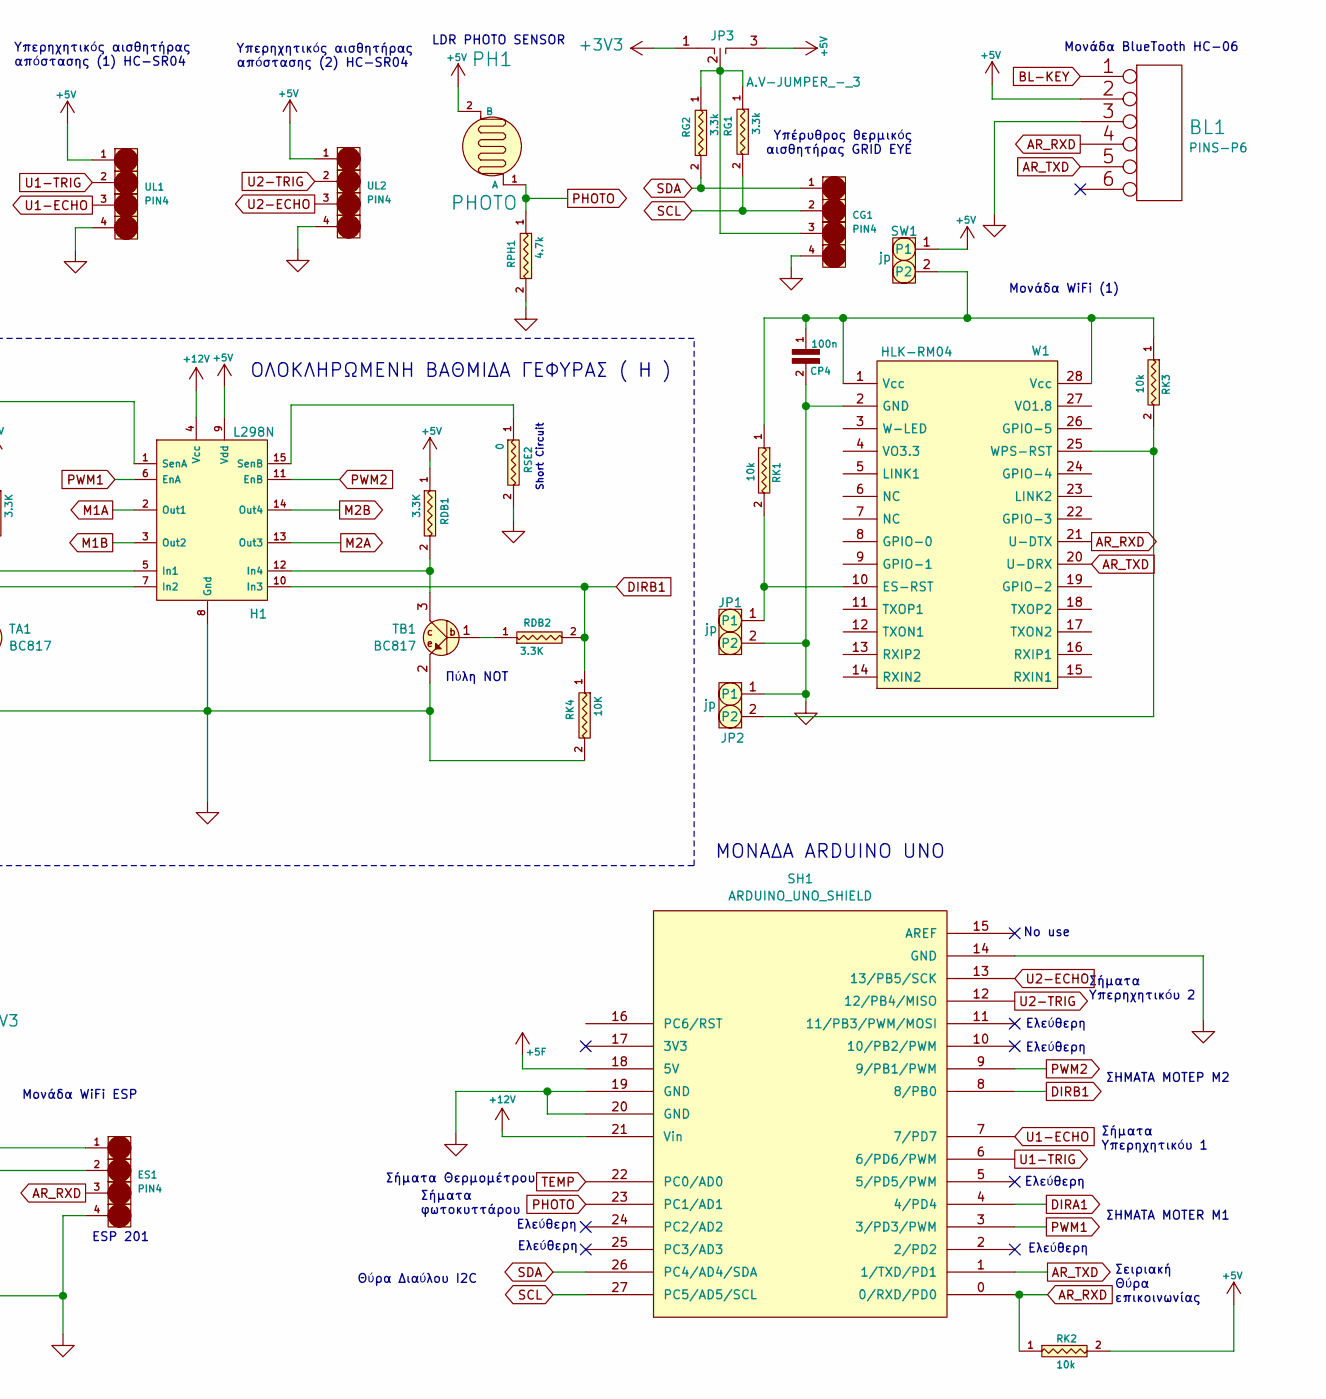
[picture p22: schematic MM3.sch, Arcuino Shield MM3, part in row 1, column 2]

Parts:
BL1: PINS-P6; AV.STR-PIN-6x1
CG1: PIN4; AV.STR-MAS-4x1
CM1, CM2: 100n; AV0805
CP1: 220uF; CAP-SMD-10
CP2, CP3, CP4, CP5, CP6, CP9, CP10: 100n; AV0805
CP7, CP8: 47uf; AV1206
DB1, DB2: DF10S; Bridge-SMD
DP1: 12CWQ06; AV-D2PACK
ES1: PIN4; AV.STR-MAS-4x1
H1: L298N; Multiwat15V
JP1, JP2: jp; AV.STR-PIN-2x1
JP3: A.V-JUMPER_-_3; JP-3-MICRO
LD1, LD3: RED; PLCC2
LD2, LD4: YELLOW; PLCC2
MC1, MC2: CLEM-2P; AV.STR-MAS-2x1
PH1: PHOTO; AV.STR-MAS-2x1
PW1: CLEM-2P; AV.STR-MAS-2x1
RDA1, RDA2: 3.3K; AV1206
RDB1, RDB2: 3.3K; AV1206
REG1: LM1086-IS-5; DPAK3
REG2: LM1086-IS-3.3; DPAK3
RG1, RG2: 3.3k; AV1206
RK1, RK2, RK3: 10k; AV1206
RK4, RK5: 10K; AV1206
RLD1, RLD2, RLD3, RLD4: 4.7K; AV1206
RPH1: 4.7k; AV1206
RS1: 1K; AV1206
RS2: 2K; AV1206
RSE1, RSE2: 0; AV1206
SH1: ARDUINO_UNO_SHIELD
SW1: jp; AV.STR-PIN-2x1
T1: LM35; AV.STR-MAS-3x1
TA1: BC817; SOT23M
TB1: BC817; SOT23M
UL1, UL2: PIN4; AV.STR-PIN-4x1
W1: HLK-RM04

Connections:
+3V3: CP8.1, CP10.1, ES1.1, JP3.1, REG2.2 (OUT)
+5F: SH1.18 (5V)
+5V: BL1.2, CP3.1, CP6.1, CP7.1, H1.9 (Vdd), JP3.3, PH1.2 (B), RDA1.1, RDB1.1, REG1.2 (OUT), RK2.2, SW1.1, T1.1 (Vdd), UL1.1, UL2.1
+12V: CP1.1, CP2.1, CP5.1, CP9.1, DB1.1 (+), DB2.1 (+), DP1.2 (K), H1.4 (Vcc), REG1.3 (IN), REG2.3 (IN), SH1.21 (Vin); also elsewhere on the board
AR_RXD: BL1.4, ES1.3, RK2.1, SH1.0 (0/RXD/PD0), W1.21 (U-DTX)
AR_TXD: BL1.5, RS1.2, SH1.1 (1/TXD/PD1), W1.20 (U-DRX)
BL-KEY: BL1.1
DIRA1: H1.5 (In1), RDA2.2, RK5.1, SH1.4 (4/PD4)
DIRB1: H1.10 (In3), RDB2.2, RK4.1, SH1.8 (8/PB0)
GND: BL1.3, CG1.4, CP1.2, CP2.2, CP3.2, CP4.2, CP5.2, CP6.2, CP7.2, CP8.2, CP9.2, CP10.2, DB1.2 (-), DB2.2 (-), ES1.4, H1.8 (Gnd), JP1.2, JP2.1, PW1.2, REG1.1 (GND), REG2.1 (GND), RK4.2, RK5.2, RPH1.2, RS2.1, RSE1.2, RSE2.2, SH1.14 (GND), SH1.19 (GND), SH1.20 (GND), T1.3 (GND), TA1.2, TB1.2, UL1.4, UL2.4, W1.2 (GND); also elsewhere on the board
M1A: CM1.1, DB1.3 (a), H1.2 (Out1), LD2.2 (A), MC1.1, RLD1.2
M1B: CM1.2, DB1.4 (a), H1.3 (Out2), LD1.2 (A), MC1.2, RLD2.1
M2A: CM2.1, DB2.3 (a), H1.13 (Out3), LD4.2 (A), MC2.1, RLD3.2; also elsewhere on the board
M2B: CM2.2, DB2.4 (a), H1.14 (Out4), LD3.2 (A), MC2.2, RLD4.1; also elsewhere on the board
unnamed: CG1.3, JP3.2, RG1.1, RG2.1
unnamed: CP4.1, RK1.1, RK3.1, SW1.2, W1.1 (Vcc), W1.28 (Vcc)
unnamed: DP1.1 (A1), DP1.3 (A2), PW1.1
unnamed: ES1.2, RS1.1, RS2.2
unnamed: H1.1 (SenA), RSE1.1
unnamed: H1.7 (In2), RDA1.2, TA1.3
unnamed: H1.12 (In4), RDB1.2, TB1.3
unnamed: H1.15 (SenB), RSE2.1
unnamed: JP1.1, RK1.2, W1.10 (ES-RST)
unnamed: JP2.2, RK3.2, W1.25 (WPS-RST)
unnamed: LD1.1 (K), RLD1.1
unnamed: LD2.1 (K), RLD2.2
unnamed: LD3.1 (K), RLD3.1
unnamed: LD4.1 (K), RLD4.2
unnamed: RDA2.1, TA1.1
unnamed: RDB2.1, TB1.1
PHOTO: PH1.1 (A), RPH1.1, SH1.23 (PC1/AD1)
PWM1: H1.6 (EnA), SH1.3 (3/PD3/PWM)
PWM2: H1.11 (EnB), SH1.9 (9/PB1/PWM)
SCL: CG1.2, RG1.2, SH1.27 (PC5/AD5/SCL)
SDA: CG1.1, RG2.2, SH1.26 (PC4/AD4/SDA)
TEMP: SH1.22 (PC0/AD0), T1.2 (Vout)
U1-ECHO: SH1.7 (7/PD7), UL1.3
U1-TRIG: SH1.6 (6/PD6/PWM), UL1.2
U2-ECHO: SH1.13 (13/PB5/SCK), UL2.3
U2-TRIG: SH1.12 (12/PB4/MISO), UL2.2

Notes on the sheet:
ΣΗΜΑΤΑ MOTER M1
ΣΗΜΑΤΑ ΜΟΤΕΡ M2
Υπέρυθρος θερμικός αισθητήρας GRID EYE
Αναλογικός αισθητήρας Θερμοκρασίας
LDR PHOTO SENSOR
Σήματα Θερμομέτρου
Σήματα φωτοκυττάρου
Σήματα Υπερηχητικόυ 1
Υπερηχητικός αισθητήρας απόστασης (1) HC-SR04
Υπερηχητικός αισθητήρας απόστασης (2) HC-SR04
Σήματα Υπερηχητικόυ 2
Μονάδα WiFi (1)
Μονάδα BlueTooth HC-06
ESP 201
ΒΑΘΜΙΔΑ ΕΙΣΟΔΟΥ ΤΑΣΕΩΣ
ΒΑΘΜΙΔΑ ΠΤΩΣΗΣ ΤΑΣΕΩΣ
ΒΑΘΜΙΔΕΣ ΣΥΝΔΕΣΗΣ ΜΟΤΕΡ
ΟΛΟΚΛΗΡΩΜΕΝΗ ΒΑΘΜΙΔA ΓΕΦΥΡΑΣ ( H )
ΜΟΝΑΔΑ ARDUINO UNO
Μονάδα WiFi ESP
Σειριακή Θύρα επικοινωνίας
Ελεύθερη
No use
Θύρα Διαύλου I2C
Πύλη NOT
Διαιρέτης τάσης
EEEFK1E221P or Equivalent
Short Circuit

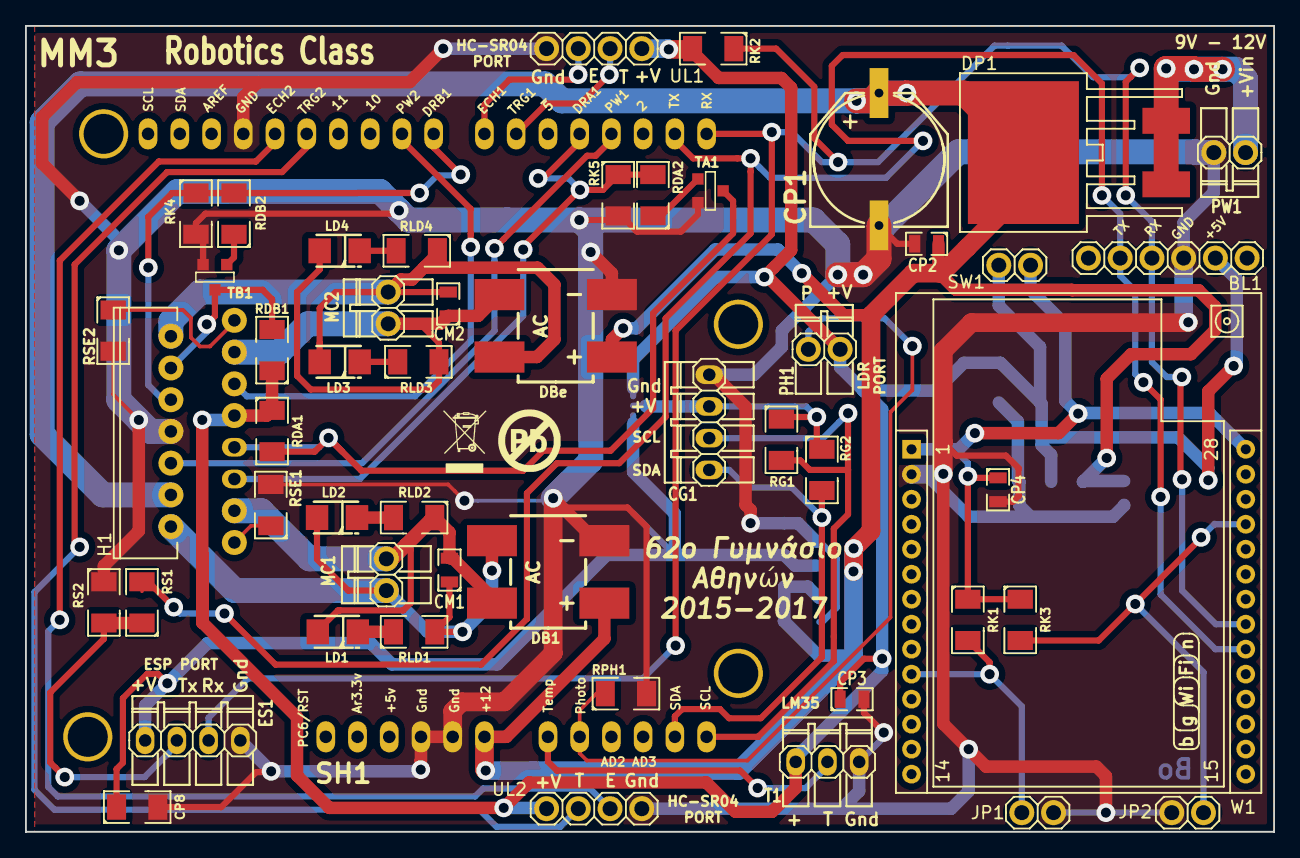
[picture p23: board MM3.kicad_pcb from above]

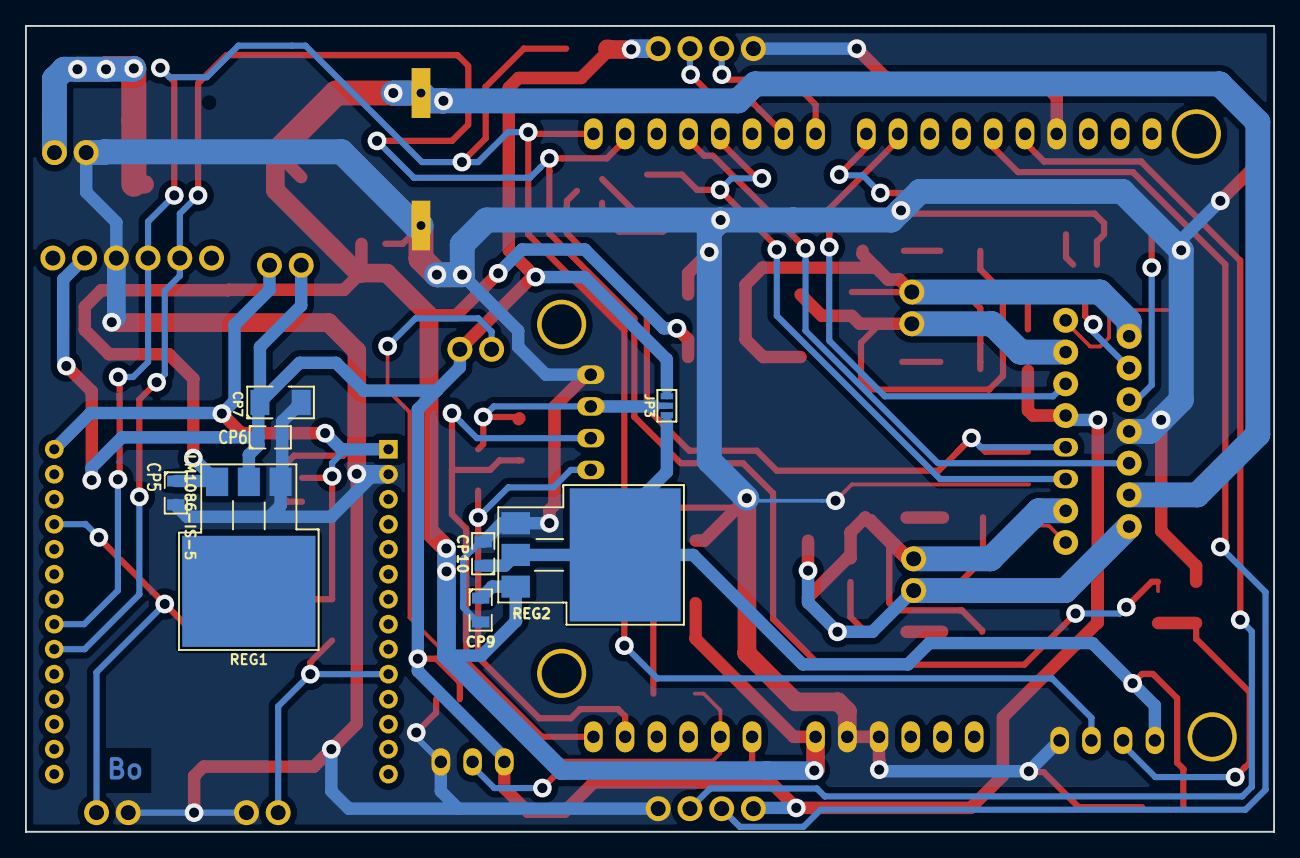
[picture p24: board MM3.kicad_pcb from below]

Board: 2 copper layers, 99.9 x 64.5 mm, 60 parts (8 on the bottom side), 38 nets.

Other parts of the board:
DBe: DF10S; Bridge-SMD

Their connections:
+12V: DBe.1; also elsewhere on the board
GND: DBe.2; also elsewhere on the board
M2A: DBe.3; also elsewhere on the board
M2B: DBe.4; also elsewhere on the board

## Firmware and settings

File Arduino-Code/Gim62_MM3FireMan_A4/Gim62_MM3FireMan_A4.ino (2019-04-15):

/*
/*
62o Γυμνάσιο Aθηνών
Εργαστήριο Ρομποτικής 2015 - 2019

Ο παρόν κώδικας γράφτηκε με σκοπό την εκπαίδευση μαθητών και δεν ενδείκνυται για άλλη χρήση.

  
Διδάσκοντες Τάξης.
Δάβος Γεώργιος ( Καθηγητής Εργαστηρίου )
Σπύρος Μπερερης ( Μέθοδοι και χρήση ARDUINO )
Αθανάσιος Βλαστός ( Πρακτική χρήση και θεωρία των ηλεκτρονικών συστημάτων ). 

Μαθητές πού λαμβάνουν μέρος στην ανάπτηξη του Project.
Βενέτης Αναστάσιος Α1(9ο Λύκειο)
Μαλανκά Αλεξάνδρα Γ3
Παναγιωτάκης Ευάγγελος Γ3
Σπυροπούλου Ζωή Γ4

Συνδέσεις
Gym62-MM3 Shield - Κύκλωμα σχεδιασμένο αποκλειστικά για εκπαιδευτική χρήση απο το 62ο Γυμνάσιο Αθηνών.

Ενσωματώνει

1. Οδηγό για δύο μοτέρ τύπου Brashed. Μέγιστο ρεύμα μοτέρ 3Α στα 12V dc.
2. Διεπαφή σύνδεσης με Grid Thermal array.
3. Ενσωματωμένο θερμόμετρο LM35
4. Ενσωματωμένο LDR. ( Φώτο-αντίσταση )
5. Δέχεται δύο αισθητήρες απόστασης αντιδιαμετρικά. HC-SR04
6. Ενσωματωμένο WiFi Router With Server
7. Δέχεται Bluetooth Module.

Wifi SSID-Gym62MM3Robot
Connection Password 12345678
Web Service UserName : admin
Web Service Pass : admin

Blue-Tooth password : 123456789
RobotCam Password 192.168.11.101 /99
Version A4_1-15/4/2019

Περιγραφή τρόπου πλοήγησης.

Το σύστημα βασίζεται σε ένα αισθητήρα παράταξης υπέρυθρων ακτίνων.
Ο αισθητήρας αντιπαράταξης δομημένος σε πίνακα 8*8, δίνοντας 64 ανεξάρτητα σημεία μέτρησης της θερμότητας.
Χωρίζοντας τον αισθητήρα σε 8 ζώνες ορίζοντα, ό παρών κώδικας ανιχνεύει τον ορίζοντα στον οποίο εμφανίζεται η μέγιστη θερμοκρασία
Με βάση τον επιλεγμένο ορίζοντα, το όχημα μεταβάλει την ταχύτητα των ερπυστριών συνεχώς, αναλογικά σε σχέση πάντα με την θέση της μέγιστης θερμοκρασίας στον επιλεγμένο ορίζοντα.
Αυτή ή συνεχώς μεταβαλλόμενη ταχύτητα των ερπυστριών οδηγεί με μεγάλη ακρίβεια το όχημα στην θέση της πυρκαϊάς.   

*/
#include <Wire.h> // Essensial Library for I2C comunication

// Ορισμοί κίνησης Μοτέρ
#define FORWARD 0 // Ο μεταγλωττιστής όπου βρίσκει την λέξη FORWARD την αντικαθηστά με το 0
#define REVERSE 1 // Ο μεταγλωττιστής όπου βρίσκει την λέξη REVERSE την αντικαθηστά με το 1
#define LEFT 1    // Ο μεταγλωττιστής όπου βρίσκει την λέξη LEFT την αντικαθηστά με το 1
#define RIGHT 0   // Ο μεταγλωττιστής όπου βρίσκει την λέξη RIGHT την αντικαθηστά με το 0
#define ON 1      // Ο μεταγλωττιστής όπου βρίσκει την λέξη ON την αντικαθηστά με το 1
#define OFF 0     // Ο μεταγλωττιστής όπου βρίσκει την λέξη OFF την αντικαθηστά με το 0

#define PWM_L  3  // Ο μεταγλωττιστής όπου βρίσκει την λέξη PWM_L την αντικαθηστά με το 3 πού είναι το pin ~3 στο Arduino
                  // Το pin 3 παράγει αναλογική έξοδο τύπου PWM 0-255 και ρυθμήζει την ταχήτητα του Αριστερού Μοτέρ. ( Left ) 

#define PWM_R  9  // Ο μεταγλωττιστής όπου βρίσκει την λέξη PWM_R την αντικαθηστά με το 9 πού είναι το pin ~9 στο Arduino
                  // Το pin 9 παράγει αναλογική έξοδο τύπου PWM 0-255 και ρυθμήζει την ταχήτητα του Δεξιού Μοτέρ. ( Right ) 
                  
#define DIR_L  4  // Ο μεταγλωττιστής όπου βρίσκει την λέξη DIR_L την αντικαθηστά με το 4 πού είναι το pin 4 στο Arduino
                  // Το pin 4 παράγει ψηφιακή έξοδο τύπου 0 ή 1 και ρυθμήζει την κατεύθηνση του Αριστερού Μοτέρ. ( Left ) 
                  

#define DIR_R  8  // Ο μεταγλωττιστής όπου βρίσκει την λέξη DIR_R την αντικαθηστά με το 8 πού είναι το pin 8 στο Arduino
                  // Το pin 8 παράγει ψηφιακή έξοδο τύπου 0 ή 1 και ρυθμήζει την κατεύθηνση του Δεξιού Μοτέρ. ( Right ) 
                   
// Ορισμοί υπερηχητικών αισθητήρων απόστασης  
#define UltraTrigR 6  // Ο μεταγλωττιστής όπου βρίσκει την λέξη UltraTrigR την αντικαθηστά με το 6 πού είναι το pin 6 στο Arduino
                      // Το pin 6 παράγει ψηφιακή έξοδο τύπου 0 ή 1 και ενεργοποιεί τον πίσω αισθητήρα ( Triger - Rear ) 

#define UltraEchoR 7 // Ο μεταγλωττιστής όπου βρίσκει την λέξη UltraEchoR την αντικαθηστά με το 7 πού είναι το pin 7 στο Arduino
                      // Το pin 7 δέχεται ψηφιακή είσοδο τύπου 0 ή 1 και για την μέτρηση της απόστασης απο των πίσω αισθητήρα ( Echo - Rear ) 
                      
#define UltraTrigF 12 // Ο μεταγλωττιστής όπου βρίσκει την λέξη UltraTrigF την αντικαθηστά με το 12 πού είναι το pin 12 στο Arduino
                      // Το pin 12 παράγει ψηφιακή έξοδο τύπου 0 ή 1 και ενεργοποιεί τον μπροστινό αισθητήρα ( Triger - Front ) 
                      
#define UltraEchoF 13 // Ο μεταγλωττιστής όπου βρίσκει την λέξη UltraEchoF την αντικαθηστά με το 13 πού είναι το pin 13 στο Arduino
                      // Το pin 13 δέχεται ψηφιακή είσοδο τύπου 0 ή 1 και για την μέτρηση της απόστασης απο των μπροστινό αισθητήρα ( Echo - Front ) 

// Άλλοι Ορισμοί 
#define Lm35Pin  0 // Ο μεταγλωττιστής όπου βρίσκει την λέξη Lm35Pin την αντικαθηστά με το 0 πού είναι το pin A0 στο Arduino
                  // Το pin A0 Διαβάζει αναλογική είσοδο τύπου 0-255 ανάλογα με την θερμοκρασία του περιβάλοντος 

#define LdrPin  1 // Ο μεταγλωττιστής όπου βρίσκει την λέξη LdrPin την αντικαθηστά με το 1 πού είναι το pin A1 στο Arduino
                  // Το pin A1 Διαβάζει αναλογική είσοδο τύπου 0-255 ανάλογα με την φωτεινότητα του περιβάλοντος 

#define P_Delay 10 // protocoll delay in ms
// Ορισμός διευθηνσης GrifEye
#define GridDeviceAddress 0b1101001

/*Συναρτήσεις και ρουτίνες προγράμματος */
void Gym62_PinSetup(void); // Ρυθμίζει τις λειτουργίες I/O του Arduino σε σχέση με το Gym62 Shield
void Gym62_ObjtacleAvoid(void);// Αποφυγή εμποδίων 
void Gym62_RobotAction(void); // Αποφασιζει αν θα τεθεί σε κήνηση.
void Gym62_CheckCommands (void); // Ελέγχει θήρα Uart και διαβάζει το πρωτόκολλο εντολών εισόδου
void Gym62_GetGridRow(unsigned char ,  float *); // Διαβάζει τα δεδομένα από μία δεδομένη γραμμή θερμικών του GridEye
unsigned int Gym62_GetThermalData (void); // Διαβάζει όλα τα δεδομένα του αισθητήρα Grid Thermal Array και τα τοποθετεί σε πινακα μνήμης για επεξεργασία
void Gym62_DirectionSet (unsigned char ,int ); // θέτει το όχημα σε κίνηση ή ακινησία στην καθορισμένη κατεύθυνση και διεύθυνση
void Gym62_MotorsMove(unsigned char ,unsigned char,unsigned char ,unsigned char ); // Θέτει την ταχύτητα και την φορά περιστροφής των κινητήρων, ανάλογα με τις εντολές εισόδου.   
unsigned int Gym62_GetDistance (unsigned char); // Διαβάζει και επιστρέφει την απόσταση των αντικειμένων από το όχημα από μπροστά και από πίσω.
void Gym62_SendThermalData(void); // απόστέλει στην Uart τα δεδομένα του θερμικού αισθητήρα. 
void Gym62_SendMetricsData(void); // αποστέλλει στην Uart τα δεδομένα κίνησης και περιβάλλοντος του οχήματος. 
void Gym62_CalculateThermalLine(float *); // Υπολογίζει την θερμική γραμμή με την μέγιστη θερμοκρασία στο πεδίο και βρίσκει το σημείο κατεύθυνσης.
float Gym62_GetGridIntTemp(void); // διαβάζει την εσωτερική θερμοκρασία του Αισθητήρα για να συγκρίνει με τις ακτινοβολούμενες θερμότητες.
bool Gym62_On_Timer(unsigned int); // Free Run timer working with flags
bool Gym62_Off_Timer(unsigned int); // Free Run timer working with flags


// Ορισμός Μεταβλητών
unsigned char RunningLspeed=255; // Μεταβλητή ταχύτητας αριστερού μοτέρ.
unsigned char RunningRspeed=255; // Μεταβλητή ταχύτητας δεξιού μοτέρ.
float InternalTemp=10; // Μεταβλητή εσωτερικής θερμοκρασίας αισθητήρα θερμοτητας.
float TopTemperature=10; // Μεταβλητή θερμοκρασίας περιβάλοντος.
unsigned int Light=10; // Ambient Light

float GridMatrix[8][8]; // Πίνακας Χ,Υ τιμών θερμοκρασιών
float GridLineY[8]; // Πίνακας ανάγνωσης γραμμής θερμοκρασιών αισθητήρα Grid  
float GridMaxLine[8]; // Πίνακας τις γραμμής όπου εμφανίζεται ή μέγιστη τιμή θερμότητας

//float ThermalLine[8];
int ThermalPeak[8]; // δείχνει τη θέση της υψηλότερης θερμοκρασίας με 1
float TempDiff[8];

unsigned char SerialByte=0;
char Buffer[10];
unsigned char BufferCnt=0;
unsigned int Number=0;
unsigned char DataToSend=0;
unsigned char RobotSpeed=250; // τελική ταχύτητα ρομπότ
unsigned char SetRobotSpeed=250; // επιλεγμένη ταχύτητα ρομπότ
int X_Address;
int PeakPointer=0;
unsigned char SpeedL=0;
unsigned char SpeedR=0;
int Direction='F';
int TempTriger=36;
float TrigerDiff=0;  
int LookUpTable[8]={-100,-75,-50,-25,25,50,75,100}; // Πίνακας με το ποσοστό της ταχύτητας των ερπυστριών σε σχέση με την θέση της μέγηστης θερμότητας στον ορίζοντα
unsigned int DistanceGetFD=50;
unsigned int DistanceGetBD=50;
unsigned int DistanceSetFD=10;
unsigned int DistanceSetBD=10;

unsigned int TimerMove=100;
unsigned int TimerStop=500;
bool FireFlag=0; 
bool AutoStartFlag=0;
bool MoveFlag=1;

unsigned long On_TmrNowVal=0;
unsigned long On_TmrPreVal=0;
bool Tmr1Exp_Flag=0;
bool On_TmrEn_Flag=0;
unsigned long Off_TmrNowVal=0;           
unsigned long Off_TmrPreVal=0;
bool Tmr2Exp_Flag=0;
bool Off_TmrEn_Flag=0;

bool GotDataCpl_Flag=false;
bool GotDataCpr_Flag=false;

bool ManualFront_Flag=false;
bool ManualBack_Flag=false;
bool ManualRight_Flag=false;
bool ManualLeft_Flag=false;

void setup ()
{
  Wire.begin(); // συδνέστε το δίαυλο i2c(διεύθηνση προαιρετική για master)
  Serial.begin(115200); 
  Gym62_PinSetup(); //  εισαγωγή ασπίδας Gym62
  
   
}

void loop ()
{


Gym62_GetThermalData(); // Διάβασε το Grid Eye και βάλτε το αποτέλεσμα σε ένα πίνακα 
InternalTemp=Gym62_GetGridIntTemp(); // Διάβασε την εσωτερίκη θερμοκρασία του Grid Eye

TrigerDiff=TempTriger-InternalTemp;  // Υπολόγισε την διαφορά της θερμοκρασίας πυροδοτησης από την εσωτερική.   
if (TempTriger<0) TempTriger=0;

Gym62_CalculateThermalLine(GridMaxLine); // υπολόγισε τόν ορίζοντα θερμοτήτων
Gym62_RobotAction(); // Πλοηγήσου με βάση τον ορίζοντα θερμοτήτων 

DistanceGetFD=Gym62_GetDistance('F'); // διάβασε μπροστινή απόσταση
//DistanceGetBD=Gym62_GetDistance('R'); // διάβασε πισινή απόσταση

if (DistanceGetFD<DistanceSetFD) { MoveFlag=0; Gym62_ObjtacleAvoid();} // Αν υπάρχει εμπόδιο μπροστά, απέφευγε το
//if (DistanceGetBD<DistanceSetBD) { MoveFlag=0; Gym62_ObjtacleAvoid();} // Αν υπάρχει εμπόδιο μπροστά, απέφευγε το

if (AutoStartFlag==false) // Αν βρίσκεσαι σε αναμονή επιτρέπεται ή χειροκίνητη λειτουργία
{
  if (ManualFront_Flag==true) 
  {
    Gym62_MotorsMove('F',RobotSpeed,'F',RobotSpeed);
  }
  else if (ManualBack_Flag==true)
  {
    Gym62_MotorsMove('R',RobotSpeed,'R',RobotSpeed);
  }
  else if (ManualRight_Flag==true)
  {
    Gym62_MotorsMove('F',RobotSpeed-RobotSpeed*50/100,'R',RobotSpeed-RobotSpeed*50/100);
  }
  else if (ManualLeft_Flag==true)
  {
    Gym62_MotorsMove('R',RobotSpeed-RobotSpeed*50/100,'F',RobotSpeed-RobotSpeed*50/100);
  }

}

Light=analogRead(LdrPin); // δίαβασε Light Dependent Resistor ( Φωτοκύταρο )
TopTemperature=analogRead(Lm35Pin)/2; // διάβασε θερμόμετρο ατμοσφαιρικής θερμοκρασίας LM35

Gym62_SendMetricsData(); // Αποστολή δεδομενων μετρησεων χρησιμοποιώντας το πρωτόκολλο
Gym62_SendThermalData(); // Αποστολη πίνακα θερμικών φωρτίων και ορίζοντα θερμικής γραμμής χρησιμοποιώντας το πρωτόκολλο
Gym62_CheckCommands(); // Ελεγχος για δεδομενα στο σειριακο buffer ( δεδομένα απομακρισμένου ελέγχου )

  

}// loop


/**********************************************************************************************************/
void Gym62_PinSetup(void)
{
  /* 
   *  Ρυθμίζει τις λειτουργίες I/O του Arduino σε σχέση με το Gym62 Shield
   */
  
  
  // H-Bridge Port Settings
  pinMode(PWM_L, OUTPUT);  
  pinMode(PWM_R, OUTPUT);
  pinMode(DIR_L, OUTPUT);
  pinMode(DIR_R, OUTPUT);
  // ορίστε την αρχική κατάσταση των ηλεκτρικών μοτέρ
  analogWrite(PWM_L, 0);  //ρυθμίστε τα δύο μοτέρ να λειτουργούν στο 0
  analogWrite(PWM_R,0);  
  
  // Distance Sensors Port Settings
  pinMode(UltraTrigF, OUTPUT);     // ενεργοποιήστε το triger του μπροστινού αισθητήρα 
  pinMode(UltraEchoF, INPUT);     // αρχικοποιήστε την ακίδα Echo του μπροστινού αισθητήρα 
  pinMode(UltraTrigR, OUTPUT);     // αρχικοποιήστε το triger του μπροστινού αισθητήρα 
  pinMode(UltraEchoR, INPUT);     // αρχικοποιήστε την ακίδα Echo του μπροστινού αισθητήρα 
 
}


void Gym62_RobotAction(void)
{
  /*
   * Σε αυτή την ρουτινα το όχημα αποφασιζει αν θα κινηθεί ή οχι 
   */
  // χρησιμοποιήστε μια συνθήκη για να λειτουργήσει χειροκίνητα ή αυτόματα( AutoStartFlag )
  if (FireFlag==true && AutoStartFlag==true && MoveFlag==true   )
  { // φωτιά εντοπίστηκε το ρομπότ κινείται προς τη φωτιά
    RobotSpeed=SetRobotSpeed;  
    Gym62_DirectionSet (Direction,X_Address);
    Gym62_On_Timer(0); // σαφείς χρονομετρητές αναζήτησης 
    Gym62_Off_Timer(0);
    Off_TmrEn_Flag=true; // ενεργοποιήστε το διακόπτη
  }
  
  else if (AutoStartFlag==true && MoveFlag==true) // φωτιά δεν εντοπίστηκε το ρομπότ ενεργοποιεί την λειτουργεία αναζήτησης 
    {
      RobotSpeed=180; // θέστε την ταχύτητα σταθερά 180
     
      if (Off_TmrEn_Flag==true && Gym62_Off_Timer(TimerStop)==true) // δοκιμάστε αν η Gym62_On_Timer είναι ενεργοποιημένη και αν έχει επιτευχθεί η επιθυμητή τιμή 
      {
        // if yes start motors        
        Gym62_MotorsMove('F',100,'R',100); // οι κινητήρες ξεκινούν 
        Off_TmrEn_Flag=false;  // απενεργοποιήση χρονοδιακόπτη  
        On_TmrEn_Flag=true; // ενεργοποιήσε Gym62_On_Timer 
        Gym62_On_Timer(0); // διαγράψτε το χρονόμετρο για να ξεκινήσει καινούργια sesion
      }
      

      if (On_TmrEn_Flag==true && Gym62_On_Timer(TimerMove)==true) // δοκιμάστε αν Gym62_On_Timer είναι ενεργοποιημένη και αν έχει επιτευχθεί η επιθυμητή τιμή 
      {
        //αν ναι σταμάτα τα μοτέρ 
        Gym62_MotorsMove('S',120,'S',160);
        On_TmrEn_Flag=false; // απενεργοποιήστε Gym62_On_Timer 
        Off_TmrEn_Flag=true; // ενεργοποιήστε Gym62_Off_Timer 
        Gym62_Off_Timer(0);   // διαγράψτε το χρονόμετρο για να ξεκινήσει καινούργια sesion 
      }
  
    }//if (AutoStartFlag==1)
    else //if (AutoStartFlag==0)
      { // το ρομπότ βρίσκεται σε λειτουργία αναμονής ( Initial condition )
      Gym62_MotorsMove('S',120,'S',160); // σταματήστε τα μοτέρ 
      Off_TmrEn_Flag=true; //ενεργοποιήστε το χρονοδιακόπτη
      Gym62_On_Timer(0); // σαφείς χρονομετρητές αναζήτησης 
      Gym62_Off_Timer(0);
      }

   
}// Gym62_RobotAction


void Gym62_ObjtacleAvoid(void)
{
 // Ρουτίνα αποφυγής εμποδίων 

 int TempSpeed=0;
 TempSpeed=RobotSpeed*80/100;
 if (MoveFlag==1) {
 return;
 }
Gym62_MotorsMove('S',0,'S',0);
delay (200);
Gym62_MotorsMove('R',RobotSpeed-TempSpeed,'R',RobotSpeed);
delay (500);
Gym62_MotorsMove('S',0,'S',0);
delay (200);
Gym62_MotorsMove('F',RobotSpeed,'F',RobotSpeed);
delay(500);
Gym62_MotorsMove('S',0,'S',0);
MoveFlag=1;
 
}


void Gym62_CheckCommands (void)
{
  /* 
   *  Ελέγχει θήρα Uart και διαβάζει το πρωτόκολλο εντολών εισόδου
   */
  char n;
  int temp;
  int Counter;
  int data;
  char SerialData[10];
  String Str;
  String NumStr;
   //ανάγνωση πρωτοκόλλου από σειριακή μέθοδο 
if(Serial.available()>4) // ελέγχει αν υπάρχουν περισσότερα από 4 bytes διαθέσιμα
{
  Counter=Serial.available(); // αντιγράψτε το μήκος των δεδομένων

  for (n=0;n<Counter;n++) 
  {
    data=Serial.read(); // διάβασε τα δεδομένα και πρόσθεστα στον πίνακα 
    Str+=(char)data; // ως χαρακτήρες
  }

    
  if (Str.startsWith("*Tr-") )
  {
    NumStr=Str.substring(4); //αριθμός αντιγράψων στο string από την θέση
    TempTriger=NumStr.toFloat(); // μετατρέψτε τον αρθμό του string σε float ή ακέραιο
    return;
  }
  
  if (Str.startsWith("*Tm-") )
  {
    NumStr=Str.substring(4);
    TimerMove=NumStr.toInt();
    return;
  }
  
  if (Str.startsWith("*Ts-"))
  {
    NumStr=Str.substring(4);
    TimerStop=NumStr.toInt();
    return;
  }
  
  if (Str.startsWith("*Sp-") )
  {
    NumStr=Str.substring(4);
    SetRobotSpeed=NumStr.toInt();
    RobotSpeed=SetRobotSpeed;
    return;
  }
  
 if (Str.startsWith("*Str")) 
 { 
  AutoStartFlag=1;
  return;
  }
 if (Str.startsWith("*Stp"))
 {
  AutoStartFlag=0;
   return;
  }

 if (Str.startsWith("*Fwd"))
          {
            ManualFront_Flag=true; 
            ManualBack_Flag=false; 
            ManualRight_Flag=false;
            ManualLeft_Flag=false;
            return;
          }  
if (Str.startsWith("*Bwd"))
          {
            ManualFront_Flag=false; 
            ManualBack_Flag=true; 
            ManualRight_Flag=false;
            ManualLeft_Flag=false;  
            return;
          }
if (Str.startsWith("*Rwd"))
          {
            ManualFront_Flag=false; 
            ManualBack_Flag=false; 
            ManualRight_Flag=true;
            ManualLeft_Flag=false;  
            return;
          }
if (Str.startsWith("*Lwd"))
          {
            ManualFront_Flag=false; 
            ManualBack_Flag=false; 
            ManualRight_Flag=false;
            ManualLeft_Flag=true;            
            return;
          }
if (Str.startsWith("*Swd"))
          {
            ManualFront_Flag=false; 
            ManualBack_Flag=false; 
            ManualRight_Flag=false;
            ManualLeft_Flag=false; 
            return;           
          }

if (Str.startsWith("*Df-"))
  {
    NumStr=Str.substring(4);
    DistanceSetFD=NumStr.toInt();
    return;
  } 
  
  if (Str.startsWith("*Db-"))
  {
    NumStr=Str.substring(4);
    DistanceSetBD=NumStr.toInt();
    return;
  }
Serial.flush();

  
  
  //AutoStartFlag=1;
 

}   

  
}// Gym62_CheckCommands

/**********************************************************************************************************/
void Gym62_SendMetricsData(void)
{

/*
 * αποστέλλει στην Uart τα δεδομένα κίνησης και περιβάλλοντος του οχήματος. 
 * 
 */
  
  String MessagePost;
  String Temp;

   
    Temp=String(TopTemperature,1);
    MessagePost=String("!tmp-"+Temp);
    Serial.println(MessagePost);
    delay(P_Delay);

    Temp=String(Light,DEC);
    MessagePost=String("!lgt-"+Temp);
    Serial.println(MessagePost);
    delay(P_Delay);

    Temp=String(SpeedR,DEC); 
    MessagePost=String("!spr-"+Temp);
    Serial.println(MessagePost);
    delay(P_Delay);

    Temp=String(SpeedL,DEC);
    MessagePost=String("!spl-"+Temp);
    Serial.println(MessagePost);
    delay(P_Delay);

    Temp=String(DistanceGetFD,DEC);
    MessagePost=String("!dtf-"+Temp);
    Serial.println(MessagePost);
    delay(P_Delay);

    Temp=String(DistanceGetBD,DEC);
    MessagePost=String("!dtb-"+Temp);
    Serial.println(MessagePost);
    delay(P_Delay);
    
       
    Temp=String(InternalTemp,1);
    MessagePost=String("!htt-"+Temp);
    Serial.println(MessagePost);
    delay(P_Delay);

   
    Temp=String(SetRobotSpeed,DEC);
    MessagePost=String("!spd-"+Temp);
    Serial.println(MessagePost);  
    delay(P_Delay);

  

    Temp=String(TempTriger,DEC);
    MessagePost=String("!trg-"+Temp);
    Serial.println(MessagePost);
    delay(P_Delay);
}// Send metrics data

/**********************************************************************************************************/
void Gym62_SendThermalData(void)
{
  /* 
   * απόστέλει στην Uart τα δεδομένα του θερμικού αισθητήρα.  
   * 
   */
unsigned int x;
unsigned int y;
String StartString;
String SendMaxString;
String SendPtrString;
String RowNum;
String TempStr;

// πρώτα στείλε δεδομένα θερμοκρασίας
for(y=0; y<8; y++) // κάντε για όλες τις τιμές y από 0 έως 7
  {
  RowNum=String(y); //μετατρέψτε τον αριθμό y σε string χαρακτήρων και βάλτε τον στη μεταβλητή Num 
  StartString=String("!ro"+RowNum); // συνθέστε το string έναρξης  
  Serial.print(StartString);
  for (x=0;x<8;x++)
    {
      TempStr=String(GridMatrix[x][y],1); // μετατρέψτε τα δεδομένα float σε string με ένα δεκαδικό ψηφίο  
      Serial.print("-"+TempStr);
        
    }//for x 
    Serial.println();     
    //Serial.print('\r'+'\n');     
  delay(P_Delay); 
  }// for y


  // Δεύτερον στείλτε το GridMaxLine. Αυτή είναι η σειρά με τη μέγιστη θερμοκρασία στη matrix
  StartString=String("!hrz"); // συνθέστε το sting έναρξης
  for (x=0;x<8;x++)
  {
     TempStr=String(GridMaxLine[x],1); // μετατρέψτε τα δεδομένα float σε string με ένα δεκαδικό ψηφίο
      SendMaxString=String(SendMaxString+"-"+TempStr); // συνθέστε το string θερμικών δεδομένων και προσθέστε το στην αρχή του string         
  }//for x 
  Serial.println(StartString+SendMaxString);// String sould be : !hrz-00.0-00.0-00.0-00.0-00.0-00.0-00.0-00.0 
  //Serial.print(StartString+SendString+'\r'+'\n');// String sould be : !hrz-00.0-00.0-00.0-00.0-00.0-00.0-00.0-00.0 
  delay(P_Delay);

  // Τρίτον στείλε το Pointer table. Αυτό είναι το υπολογισμένο σημείο φωτιάς στον ορίζοντα
  StartString=String("!ptr"); // συνθέστε το string  έναρξης 
  for (x=0;x<8;x++)
  {
     TempStr=String(ThermalPeak[x]); // 
      SendPtrString=String(SendPtrString+"-"+TempStr); // συνθέστε το string θερμικών δεδομένων και προσθέστε το στην αρχή του string        
  }//for x 
  Serial.println(StartString+SendPtrString);// το string πρέπει να είναι : !ptr-0-0-0-0-0-0-0-0 
  delay(P_Delay);

  

}// SentThermalData



/**********************************************************************************************************/
void Gym62_DirectionSet (unsigned char Dir,int address)
{

/* 
 * θέτει το όχημα σε κίνηση ή ακινησία στην καθορισμένη κατεύθυνση και διεύθυνση
 * Με βάση την επιλεγμένη ταχύτητα του οχήματος υπολογίζεται ή μείωση τις ταχύτητας της μίας ερπύστριας ανάλογα με την διεύθυνση και κατεύθυνση εισόδου
 * Η μία ερπύστρια κινείται με την μέγιστη ταχύτητα και ή άλλη με την υπολογισμένη.
*/

int AddressSpeed=0; // Αυτός ο καταχωρητής αποθηκεύει την υπολογισμένη ταχύτητα με την οποία θα κινηθεί ή μεταβαλλόμενη ερπύστρια  

if(address>=0) AddressSpeed = RobotSpeed - ( (address*RobotSpeed)/100 );
else  AddressSpeed = RobotSpeed + ( (address*RobotSpeed)/100 );

if (AddressSpeed==0) AddressSpeed=30; // Η ερπύστρια δεν μπορεί να είναι ακίνητη για λόγους προστασίας από τις τριβές.

 
if ( (Dir=='F' || Dir=='f') && address>=0 ) Gym62_MotorsMove('F',RobotSpeed,'F',AddressSpeed);
   else if ( (Dir=='F' || Dir=='f') && address<0 ) Gym62_MotorsMove('F',AddressSpeed,'F',RobotSpeed);

 
if ( (Dir=='R' || Dir=='r') && address>=0 ) Gym62_MotorsMove('R',AddressSpeed,'R',RobotSpeed);
   else if ( (Dir=='R' || Dir=='r') && address<0 )Gym62_MotorsMove('R',RobotSpeed,'R',AddressSpeed);


 if ( Dir=='S' || Dir=='S') Gym62_MotorsMove('S',0,'S',0);  
  
 }
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

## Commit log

2019-03-22 Adding Arduino Shield Gym62-MM3 Design Files
    [MM3-2019-02-19-09-46-50.sch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]
2019-03-26 Add files via upload
    3D Renderings Of Gym62 MM3 Arduino Shield
2019-04-15 Adding Arduino Code and Hardware Description
2019-04-21 Create datashets.md
    Εδώ περιλαμβάνονται τα data sheets των ηλεκτρονικών υποσυστημάτων που έχουν χρησιμοποιηθεί στο έργο 62GYM-FIREMAN
